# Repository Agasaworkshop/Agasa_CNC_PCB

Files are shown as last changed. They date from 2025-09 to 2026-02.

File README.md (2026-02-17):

# PCB MILLING CNC OVERVIEW  



I've decided to make this CNC from spare parts to see if I was up to the challenge. This was very time-consuming, and it is still a work in progress, but it is enough for a first publication, to see if people like it and maybe contribute.
****The total cost is around 150€, it also requires several hours of printing and assembly.****  
[Here you can find a video about it](https://www.youtube.com/watch?v=syjpmd4Yy7Q)

This project aims to create an affordable CNC that can be built with many common parts you might already have lying around: [here you can find the bill of materials.](https://docs.google.com/spreadsheets/d/1UYvKP2MYEV8sfaGlQmCoOGCL_2WACBQjZGL0-ml8eyc/edit?usp=sharing)

This project also needs some tools like:  
- A soldering iron
- Something to cut M8 and M4 threaded rods, like a hacksaw or Dremel (or even a bolt cutter for the M4 rod)
- M3 and M1 allen key (usually provided with the screw sets and collet).
- M8 wrench.
- Common household supplies like tweezers and scissors.
- A drill (even a weak one) to drive the M8 rods into PLA pieces and make holes.
- A hammer + small screwdriver (it is sometimes useful to drive the M4 rods into the PLA).
- Phillips screwdrivers for the screw terminals of the relay and motor driver.
- A hard brush to clean up the boards after milling. 

This machine is made to accept two common formats of copperclad board I can find online, which are 10x7cm and 5x7cm.
It is a relatively slow machine ([but it could be improved](https://github.com/Agasaworkshop/Agasa_CNC_PCB?tab=readme-ov-file#plans-for-upgrades)), and results also depends on the board quality.  
It is also very loud and requires eye protection, ear protection, and a respirator mask.

Here is a quick preview of the process of making a board (more info below):

| Step | Description | Time taken | Needs operator surveillance |
|:---|:---:|---:|---:|
| Make the PCB | use [Kicad](https://www.kicad.org/) or some other software to make the gerber files | depends on the board | Yes |
| Convert Gerber to CNC files | use [flatCam](http://flatcam.org/) (or similar) to export a gcode with the proper format | 3 minutes | Yes |
| Jog the machine to the starting point and change the bit | use gcode and the commands to set a relative origin, enable plane probing and change the bit | 5 minutes | Yes|
| Start milling | Use the commands to start the route.cnc file** | 6 minutes for plane probing and 22 minutes for the example PCB(the loud part) | No|
| Jog the machine to the starting point and change the bit | use gcode and the commands to set a relative origin, disable plane probing and change the bit| 3 minutes | Yes|
| Start drilling | Start the drill.cnc** file | 8 minutes for the example PCB | No| 
| Jog the machine to the starting point and change the bit | use gcode and the commands to set a relative origin and change the bit| 5 minutes | Yes|
| Start cutting | Start the edge.cnc** file | 20 minutes for the PCB shown*| Yes |
| Add UV mask | I would not advise making this on the CNC, I did try a bit  but it is not worth it time-wise | 10 minutes [(without CNC)](https://youtu.be/wvU2yyfH-XE?si=ILHJE20edIJDHiam) | Yes |  

*I was afraid to go too fast, so I didn’t stress test this. I used 0.3 mm passes at 250 speed (31% of max) with a 2 mm bit not meant for PCBs. Test with caution.  
**You can also run other file names. I made some specific names and commands to make it quicker for my testing. 

Here are the PCBs I refer to  


  

The third one was done by milling the solder mask, but I do not recommend it as it is quite unreliable. 

Here are some standard results on FR1 board made with the latest release (note that you can get better results, but I tried to ensure reliability):

(they all work fine)

## What to expect
I REALLY do not want to deceive anyone, this machine is not perfect at all.  

This was a project made to challenge myself and allow me to make PCBs at home, the process is a bit convoluted, the arduino code could be less clunky (even though I am limited by the Arduino Nano’s memory, I should migrate this project to a more capable board in the future).  

When drilling holes they tend to be slightly off center, it might be due to some imperfections, it does not seem to stack over time tho. 
In previous versions of the Z rails I had some problems losing some steps over long incisions but that is no longer the case.  
For reference, this is a 50-minute incision, this is close to the maximum this machine can do

Here is the board:  


Due to the size of the board, I suggest cutting deeper to ensure proper isolation. This worked reasonably well, but I had to refine 5 pads with a box cutter. (I used –0.15 mm to be sure, that is why some traces are a bit deep, I might also suggest using a 0.2mm bit and not a 0.1mm bit, especially if you don't use a soldermask to avoid bridging while soldering).  

There is also some kind of distortion (not related to lost steps) that causes some traces to deform, this is usually harmless unless it happens on the segment that closes the shape, to prevent this from causing problems I've added the "add squares" option to the patcher. It seems to work fine.   

Here you can see a board that was also cut with this machine(the bit was a bit out of whack here tho).   
    
This board is the [Detective Boys walkie talkie pin badge](https://github.com/DanieElectronics/DetectiveBoysWT) from [DanieElectronics](https://github.com/DanieElectronics)

# Assembly
Being a budget machine, it requires considerable effort on the user's part for assembly.  
Additional hardware notes can be found [here](HARDWARE_NOTES.md).
## Frame
The frame is made of hollow PLA segments reinforced with M8 threaded rods and filled with concrete.  
This creates a very rigid structure with decent tolerances, good vibration damping, and low cost. The M8 rods also help with assembly.  




## Axes
Describing the assembly of each small piece in detail would be complex and not very clear. That’s why I prepared four files: Preview.blend, Preview_x.blend, Preview_y.blend, and Preview_z.blend—each containing all 3D printed pieces and hardware in their correct positions, with [color-coded](https://docs.google.com/spreadsheets/d/1UYvKP2MYEV8sfaGlQmCoOGCL_2WACBQjZGL0-ml8eyc/edit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) hardware. 
Apply grease to all screws and guides.
Unfortunately, I am dumb enough to model in blender.  
I didn’t find a better way to display the assembly, so you will need to [download Blender](https://www.blender.org/download/) (free) to view the files.  
This also means I don’t have convenient CAD files for the project. Even the STL files come from messy Blender projects, so I will consider the STL files themselves as the source for licensing purposes.  





### Y axis
Due to the way it is mounted this axis requires a bit of care, you'll have to adjust it so that the rails are pretty consistently spaced (use a caliper to check).

### Bellows
Unfortunately, this was a bit rushed.   
You can print the bellows flat on your bed with a 0.12mm layer height.   
This will result in a sheet that can easily be folded back and forth to make the bellows. I did not add some of the features to make them easier to detach from the plate, but they can be easily cut out.   
[Here  you can find some more information on how I installed them.](Bellows.md)  

## Electronics
The electronics require some work, but it should not be a problem for anyone building PCBs.  
Here is the list of boards I used:  
3x ULN2003 stepper motor driver  
1x micro SD card reader  
1x Arduino Nano  
1x LM2596 DC to DC Buck Converter module   
1x relay module  
1x custom board (see below)  
1x custom board to distribute power (just a couple of lines of solder with all the cables going out to the various modules)
1x metal M3x10cm washer used for the motor.  
1x metal washer with a bigger diameter used on the bed.  

-I power this with a computer power supply (the 12V line). I suggest using this type of power supply, as they can be obtained cheaply or even for free from old computers and online marketplaces such as eBay or Facebook marketplace.   
-Power the ULN2003 with 12 V, along with the motor driver and the step-down module (if you use a computer PSU, you can simply connect the 5 V line).   
-Set the step-down output to 5 V, and connect the Arduino, relay, and SD card boards to it.   
-The relay is used to switch on and off the motor driver.      
-The motor driver is connected to the motor with a flyback diode and large capacitors rated for more than 12 V.    

This is the pinout of the Arduino:  

| Arduino pin | Conn. | Arduino pin | Conn. |
| :---: | :---: | :---: | :---: |
| TX1 | NC | D13 | SCK sd card board |
| RX0 | NC | 3v3 | NC |
| RST | NC | REF | NC |
| GND | OUT- stepdown | A0 | MZ IN4 |
| D2 | MY IN4 | A1 | MZ IN3 |
| D3 | MY IN3 | A2 | MZ IN2 |
| D4 | MY IN2 | A3 | MZ IN1 |
| D5 | MY IN1 | A4 | Relay S |
| D6 | MX IN4 | A5 | Z2 enable pin custom board |
| D7 | MX IN3 | A6 | switch pin on custom board  |
| D8 | MX IN2 | A7 | Z2 pin on custom board |
| D9 | MX IN1 | 5V | OUT+ stepdown |
| D10 | CS sd card board | RST | NC |
| D11 | MOSI sd card board | GND | NC |
| D12 | MISO sd card board | Vin | NC |  

NC = not connected  
MX = ULN2003 connected to the x motor  
MY = ULN2003 connected to the y motor   
MZ = ULN2003 connected to the z motor   

To check all the limit switches and the contact between the board and the motor with a few pins, I have made a little custom board on perfboard.  
Here is the schematic:  
   
I suggest adding connectors (I used JST connectors) at the positions indicated by the red boxes.  

I mounted the electronics with my [CMS](https://www.printables.com/@AgasasWorksho_391302/collections/863243) system on a printed plate (that you can find in the files)  

  

Alternatively, you could put together the circuit on perfboard like shown here:
   
Using the kicad files might help making this. 

Once the machine is ready, you could mill your own board:   
  
This board will be uploaded under the name "single sided PCB".  
Here it is mounted and working:  
   
I would advice using the board from PCBway below as a reference for the components, in alternative you can use the kicad file.  

Probably the most convenient way of doing this would be to buy one from [PCBWay](https://www.pcbway.com/) from the start, in fact they kindly sponsored me and provided me with some boards to test and I was really happy with the product, they are really well made quality boards (and I know a thing or two about making PCBs at this point) here they are, I will upload them as "double sided PCB"   
  
    
Note that I messed up the capacitor silkscreen and it's flipped, the files I upload will be corrected.   
[Here you can find the list of components.](https://docs.google.com/spreadsheets/d/1UYvKP2MYEV8sfaGlQmCoOGCL_2WACBQjZGL0-ml8eyc/edit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)  

How the washers are  mounted:   
   
You can solder tin to steel; it will flow nicely once the washer reaches a sufficient temperature. This may take some time, during which the solder will not adhere.  

# Using the machine
The code does the minimum required to make the machine work. It can read some G-code, probe the plane to compensate for a skewed board or other imperfections. Here is the list of commands:  
1 + {Gcode} = executes that Gcode.  
2 = Saves the current X, Y, Z coordinates to the offset, and considers the current position as the origin.  
3 = writes in the console the X,Y,Z coordinates, the offsets and some more stuff.  
4 = lowers the Z axis until it finds contact.  
5 = starts the "route.cnc" file.  
50 + "file_name.cnc" = starts the "file_name.cnc" file. For example, 50 route.cnc is equivalent to command 5 (max 16 characters).
51 = starts the "mask.cnc" file. It does not disable plane probing and does not perform probing; you need to have done the previous probing. (Do not shut it down after route.cnc).
52 = starts  the "drill.cnc" file, disables plane probing.  
53 = starts  the "cut.cnc" file, disables plane probing.  
6 = tries to initiate the SD card (also done at start).  
7 = prints SD card content.   
8 = homes the Z axis alone.   
9 = toggles plane probing.   
10 = toggles debug mode, which enables moving without homing.   
11 = toggles enabled and disabled holding torque.  

❕Note that the 51/52/53 commands are already tailored for their purpose and should not need you to toggle plane probing, if you use the 50 command you must disable the plane probing if you don't want it (for example if you decided to make a different drill_1.cnc file make sure to have plane probing off).

Change relative system  
21 = save solder mask relative system.  
22 = save drill relative system.  
23  = save cutting relative system.  
211 = load solder mask relative system.  
221 = load drill relative system.   
231 = load cutting relative system.  

The machine currently cannot change spindle speed. You can manually adjust it on some motor drivers. I always run it at 100%. I plan to update this; it should be fairly simple, but I’m burned out.  
The machine currently only recognizes  
G00/G01  (movement)  
M03/M05  (spindle on/off)  
G28  (home all axes)  
M220 (change stepper speed, for example "G220 80" (or "G220 S80 it's the same) will set the G01 speed as 80% of the G00 speed which is considered the fastest speed (can't go over 100% or under 0%)  
I did attempt some extra features, but the Arduino Nano is already running out of memory.  

## How to prepare the files
- Create the gerber file.  
- Import the gerber files of the engraving, holes and cuts in flatcam.  
- Select the engraving, go to isolation routing, and set the bit thickness (I use 0.1 mm, sometimes 0.2 mm). Generate the geometry and set the bit as a C-bit (even if it is actually a V-bit). Then select a cutting depth. Different boards may require different values, so you will need to experiment. On FR1 boards, a depth of -0.1 mm produced good results.   
- Set the end move and tool change Z to a low value to avoid exceeding the limits, then generate the CNC object and save the file as route.cnc. Open the CNC_file_patcher I provided and drag the file onto it; it will be patched for this machine. (Note: you can name the file anything if you plan to use the 50 command, up to 16 characters.)    
- Select the drill file, set the tool change Z and end move to 3 mm, and set the cutting depth slightly less than the PCB thickness (I use -1.35 mm on 1.4 mm boards). This prevents damaging the bed, but you will need to complete the holes manually. It is a simple and quick task. Save the file as drill.cnc (you can choose any name if you use the 50 command).   
-  Select the edge file, set the bit diameter, and use the same depth as for the drill file. I used -0.3 mm passes to avoid stressing the machine. Export it as edge.cnc (you can name it freely if you use the 50 command).   
-  Select the mask file, set the bit diameter, and use the paint tool. Set an offset—0.5 mm is recommended—but check that the mask is fully cut out given your bit diameter. The software will skip areas that are too small for the bit plus offset. Export the file as mask.cnc (you can name it freely if you use the 50 command).    

## How to operate the CNC  
‼️‼️You MUST wear personal protective equipment (PPE) when operating this machine, including eye protection, ear protection, and a respirator mask (especially for edge cutting and drilling). Work in a well-ventilated area, particularly when using FR4 boards or performing cutting operations (I don't even really recommend cutting FR4, just engraving and milling). 
 
Use commands prefixed with M only if you plan to mill the solder mask, and N only if you do not plan to mill it. Note: milling the solder mask is not recommended.    

!!As it stands, disconnecting the computer and reconnecting will lead to the Arduino resetting and losing the ability to keep going with what you were doing. Use a reliable method; I found out my phone is great at this; it can go into standby and still not lose the serial connection, and thus not reset the Arduino. 

- 1) Power up the machine with the external power supply and connect your computer or phone.  
- 2) Secure a board with all bolts, make sure the bed washer is tight. Forgetting this may damage the bit.   
- 3) Before moving, you must home the machine (it will not accept movement if not homed). Send the following over serial at 9600 baud: "1 G28". Here, 1 indicates that the following command is G-code, and G28 is the “home all axes” command.    
- 4) Jog the machine to the desired starting position using G00 (rapid movement). A good starting point is the bottom-left corner, approximately at X20 Y20. For example: "1 G00 X20 Y20".  
- M5.1.1) Secure the mask milling bit and use the 4 command to bring down the motor to the copperclad board. Save the mask relative system with 21 and home the Z axis with the 8 command.   
- M5.1.2) Secure the drilling bit and use the 4 command to bring down the motor to the copperclad board. Save the drill relative system with 22 and home the Z axis with the 8 command.  
- M5.1.3) Secure the cutting bit and use the 4 command to bring down the motor to the copperclad board. Save the cutting relative system with 23 and home the Z axis with the 8 command.  
- 5.2) Secure the engraving bit and use the 4 command to bring down the motor to the copperclad board. Save the current position as a new origin with the 2 command.
- 6) Enable plane probing with the 9 command. It should say "Prob:on" in the console.  
- 7) Start the engraving process with the 5 command. (or 50 + file name if you named the file differently)
- 8) Wait for the engraving to finish, in my experience, it is relatively safe and hands off but really loud.  
- 9) Remove the dust with a mini vacuum cleaner.  
- M10) Mount the mask milling bit. Load the relative system with command 211. Go to the starting point. Since you saved the relative system in step 5.2, use "1 G00 X0 Y0".   
- M11) Start the mask milling with 51, set the motor speed to 3% (to mill the mask you will need to be able to control the motor).  
- M12) Wait for the mask milling to compòete. This is also hands off, less loud tho.
- 13) Mount the drilling bit, set the speed to max again, disable plane probing with the 9 command.  
- M14) Load the drill relative system with 221 and go back to the origin (1 G00 X0 Y0).  
- N14) Go back to the origin (1 G00 X0 Y0). Lower the z axis with the 4 command and set a new relative system with the 2 command.  
- 15) Start the drilling process with the 52 command.
- 16) Wait for the drilling to finish. In my experience it is relatively safe and hands off but really loud.  
- 17) Remove dust.  
- 18) Secure the cutting bit.I suggest a 1mm cutting bit  
- M19) Load the cutting relative system with command 231. Set the feed speed* and return to the origin using "1 G00 X0 Y0".  
- N19) Lower the z axis with the 4 command and set a new relative system with the 2 command.  
- 20) Start the cutting process with the 53 command.  
- 21) Wait for the cut to finish. While you're at it keep an eye on it, and remove some dust. I suggest moving it with a brush and vacuuming it off the board.
- 23) Dismount the board. Scrub it with a hard brush, check continuity, drill out any remaining holes and complete the cut with a box cutter.
- N24) Add the solder mask like in [this video](https://youtu.be/wvU2yyfH-XE?si=ILHJE20edIJDHiam).

❕❕Every time you secure a new bit, you will have to check for the runout. I just look at it and spin it slowly to check, this is very finicky; it will depend on the quality of your coupler or collet.  
I still fight a lot with my coupler to get it right. Sometimes it looks fine, but it isn't. It's the biggest problem for me, and it would be solved just by finding good quality 3.17mm couplers, I yet have to find them tho.  
You can find some more details on this [here](HARDWARE_NOTES.md).

*You can set the speed of the G01 command via the M220 command, with a 1mm bit. I have seen you can actually go 100% speed at 0.3mm passes. I would still go a bit lower, like 80%. 

## Post processing
I scrub the board vigorously with a hard brush, which usually suffices. In some cases, I used 500-grit sandpaper (for metals) to fix poorly isolated pads. The process takes less than a minute in total.  
I do advise checking for continuity on your board always.  
In the worst-case scenario, you can use an X-Acto knife or box cutter to fix traces. I have worked extensively to avoid this, so it should not be necessary most of the times.  
Soldering without a solder mask is a harrowing process, so I would advise adding it as shown [here](https://youtu.be/wvU2yyfH-XE?si=ILHJE20edIJDHiam). I am not satisfied with the results of milling the mask myself, although performance depends greatly on the quality of the spring-loaded bit.  

## File patcher   
   
   
The file patcher accepts a file (simply drag and drop it onto the window), patches it, and overwrites it with the new version. Currently, it has five features that you can toggle:  
- Split segments: subdivides long segments into shorter ones (maximum 2 mm). This improves plane compensation, as the software currently creates four planes to approximate the board. Long segments spanning multiple planes can cause inaccuracies.  
- Add overlap: adds some overlap between the end of a trace and its start to improve the likelihood of correct isolation. Copper can sometimes deform and leave a bridge.
- Improve pads: merges close lines of adjacent pads to reduce the probability of ripping off the pad (especially useful for small pitches like 0.5mm). This does not currently work well with the overlap so I made it so that it toggles between the two. This feature is currently limited to horizontal and vertical pads. 
- Add squares: Add squares: due to some errors (possibly bit flexing or play in the axis), the tool may fail to properly reconnect when closing a shape. To improve reliability, this option adds a very small square at the end to ensure a proper cut.
- Extra squares: makes the square bigger to make sure. If they are problematic, the small squares are usually enough.
- Simplify shapes: this could speed up the cut a bit.  
Recommended settings are pre-checked by default.  
I plan to add the ability to customize the squares and other features in a future update.  

# Plans for upgrades
I decided to finalize the current version of the project to take a break, but I still have many improvements I want to implement.  
Here are some potential upgrades:  
1. One could tinker with the speeds, I pushed the x and y motors quite a bit already but I did not consider the z speed to be that impactful on the time. 
2. Considering the little additional cost of NEMA motors, one could decide to mount a pancake NEMA17 motor to the Z and X axis and standard NEMA17 to the Y axis. The code should be fairly simple; I would mostly care about fitting nemas to X and Y and try to get a better speed.
3. I've tested quite a bit with milling the solder mask and did not have perfect results. I currently suspect my DIY bit is not up to the task. I should investigate further but it felt like a fool's errand, knowing the other way of adding the solder mask.
4. I've fitted the bellows at the end and did not do the best job. I would love to improve on them.
5. Currently, the spindle is very loud. I'd like to figure out if I can do something about it.
6. The current spindle speed regulation is crude. If you skip milling the mask, a single speed suffices. Adding an H-bridge would simplify speed control (the motor draws about 2.5 A).  
7. I would like to test different types of plane probing to maybe make it quicker (it currently takes a total of 25 points 5 at each spot, maybe I could do just 1 for each spot).  
8. I did not tinker enough with the cutting speeds because I was a bit afraid of wrecking the machine at the finish line. I'll have to test a bit after I recover from burnout. 
9. I might want to migrate the code to a better microcontroller. I used arduino to be more accessible but its limitations did show.
10. I tinkered with adding a saving system to avoid homing all the times and to avoid losing progress if one ended up resetting the Arduino by accident. The problem was the arduino memory that was running out.
11. If I do end up changing some of the above, I would probably implement some extra G code, like spindle speed.
12. Find the best working coupler to get good alignment every time; it's the biggest problem for me.
13. I could also consider adding alignment holes to the bed to try implementing double-sided boards.

# Disclaimer
This machine involves mechanical, electrical, and operational risks. I strongly recommend using appropriate personal protective equipment (PPE mentioned above) and ensuring proper ventilation during operation.  
Keep your hands and body parts away from moving axes and the cutting tool, as the system can generate significant force.  
Be careful when wiring the power supply, especially when working with mains voltage.

This project is not certified for compliance with any safety or regulatory standards. By building, modifying, or operating this machine, you acknowledge and accept that you do so entirely at your own risk.
I shall not be held liable for any injury, damage, loss, or legal issues resulting from the use or misuse of this project.

## Extra
- This machine operates on two sizes of boards, which are 5x7 and 10x7. [I've made a little jig to score and snap the boards](https://www.printables.com/model/1377196-107-pcb-splitter), it works well with FR1, not too well with FR4 (it isn't impossible tho).  
- I did attempt some backlash compensation with disappointing results; the current code still has the remains of that (but the parameters are set to 0).

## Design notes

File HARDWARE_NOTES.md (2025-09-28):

# I've experimented quite a bit with different hardware and configurations. I would like to share my findings and ideas here:

## Collets:  
  
Here are all the collets (all 3.17mm to 3.17mm couplers or collets) I've tried:  

1. The hole had quite a big tolerance; the bit ended up being wonky most of the times it was very frustrating to correct.  
2. Same as 1  
3. It was too tight, I could not fit the bits.  
4. It had similar tollerances to 1 and 2 but the coupler nature makes it a bit easier to adjust, it's also quite heavy.  
5. This fit the bit perfectly, the only problem was that it was too tall, this prevented me from mounting.   
6. This is my current choice, it has similar problems to 4 but it's quite a lot lighter and a bit smaller.

I suggest marking one side and tightening mostly that side to both motor shaft and cutting bit to improve probability of working.  
EVERY TIME you change bit you need to check for runout, I don't have anything fancy I jsut spin the bit with my fingers and check if I see it wobble.   
Rule of thumb: if you think there is an imperceptible wobble but you're not sure, there probably is.  

## Motor springs:
These cheap stepper motors have quite a bit of play on the shaft, at the start I tought with the forces involved and the vibrations it would have been necessary to fit very stiff springs, turns out you don't need much.
I strongly suggest quick release skewer springs from bikes, they are very weak and they have the right dimensions, the larger side should be facing the motor. I've tested (and am currently running) much stiffer tower springs
and I did not notice any difference, I am a bit afraid they will wear out the motor quicker but I can't be bothered to change them back.  

## Possible alternative motors:
I've found a couple of alternative stepper motors that could fit this machine. With minor modifications you could even fit fit NEMA17 motors, this would require changing the drivers and code a bit tho. 
I've also found similar motors to these common 28byj-48 with all metal gears, those might be a good upgrade.

## Motor driver:
I'm using a relay with a big DC motor driver I had lying around but it's overkill and cluncky, one could probably fit a much cheaper and effective driver that could be piloted with the same pin as the relay and allow 
for the addition of a speed command, I will work on that in the future.

## Motor to leadscrew couplers:
I've tested a couple, I am currently mounting the clamp style ones but I think the ones with grubscrews would be better. I think the springy ones are not too good for this application I would avoid those. 

Example images of these couplers (source: AliExpress listings):
Springy couplers:  
   
Clamp style coupler:  
  
Recommended couplers:  
  

## Cutting bits:
There are a lot of different kinds of bits. I've found these to be the best (most reliable and durable):  


## Electronics:
I've tried a couple of different configurations; my CMS setup was the easiest to mount but pretty messy.  
I've also tested with making it with perfboard, it took me a lot of time to make, I don't really thinK it was worth it. If you still want to try this route the pcb I designed should be a good reference.  
I've also made a custom PCB, you could pay a service to make you one or, after mounting the machine with a different setup mount it yourself, I'll incluede a CMS module for this board in the files.  

In my design I've used 3 ULN2003; one could consider using only 2 but I did not want to push the current limits of the ICs and just decided to copy the cheap common boards. It is also quite improbable you have 3 motors and only 2 drivers.

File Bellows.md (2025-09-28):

# How to mount bellows  
This, unfortunately, is one of the weakest parts of this build. These parts are quite important to keep dust away from your sensitive lead screws and linear guides.  
In the future, I plan to mount all of them with M3 screws but as of right now you need to hot glue some of the bellows.

# Printing the bellows
You need to print these flat on the bed with 0.12mm layer height, you should get only two layers. After printing you need to bend it back and forth.

# Y bellow
Print two bellows, you will have one at each side of the carriage.
Thread the fishing line (or other wire) through the holes of the bellows and pass it through the hole in the rod holder, do this for both sides then clamp both the wires and the bellow with a screw fixed to the heatset insert of the rod holder, use two pieces of wire, cut them long and refine it later.  
To fix the other end to the carriage hotglue them, you can also cut it a bit with scissors if convinient.  
You should try to get them so that the bellow when folding tends to go down a bit.   
(You can also always glue the rod holder part too of course)   

   

Lateral view   

   

How to glue the bellow to the carriage, note that the piece right next to the glued one bends downwards  

   

How to clamp bellows and strings

Test it by moving the axis in his full range (0 to 90) at the end to see if it folds nicely, try to reposition the glued parts if not.  

# X bellow
This only has glued parts, unfortunately.  
Similar to the Y bellow you need to print two and thread the line, I used only one longer line here looping it around one of the two sides.  
Glue the string at the end of the other side like shown below.  
   

Glue the bellow to the upper lip like here and make sure to get the bellow to bend without raising up like here:  
   

Test it by moving the axis in his full range (0 to 119) at the end to see if it folds nicely, try to reposition the glued parts if not.  

# Z guard
This piece also prints as a flat sheet; bend it in the weak points and secure it to the screw heads like shown:   


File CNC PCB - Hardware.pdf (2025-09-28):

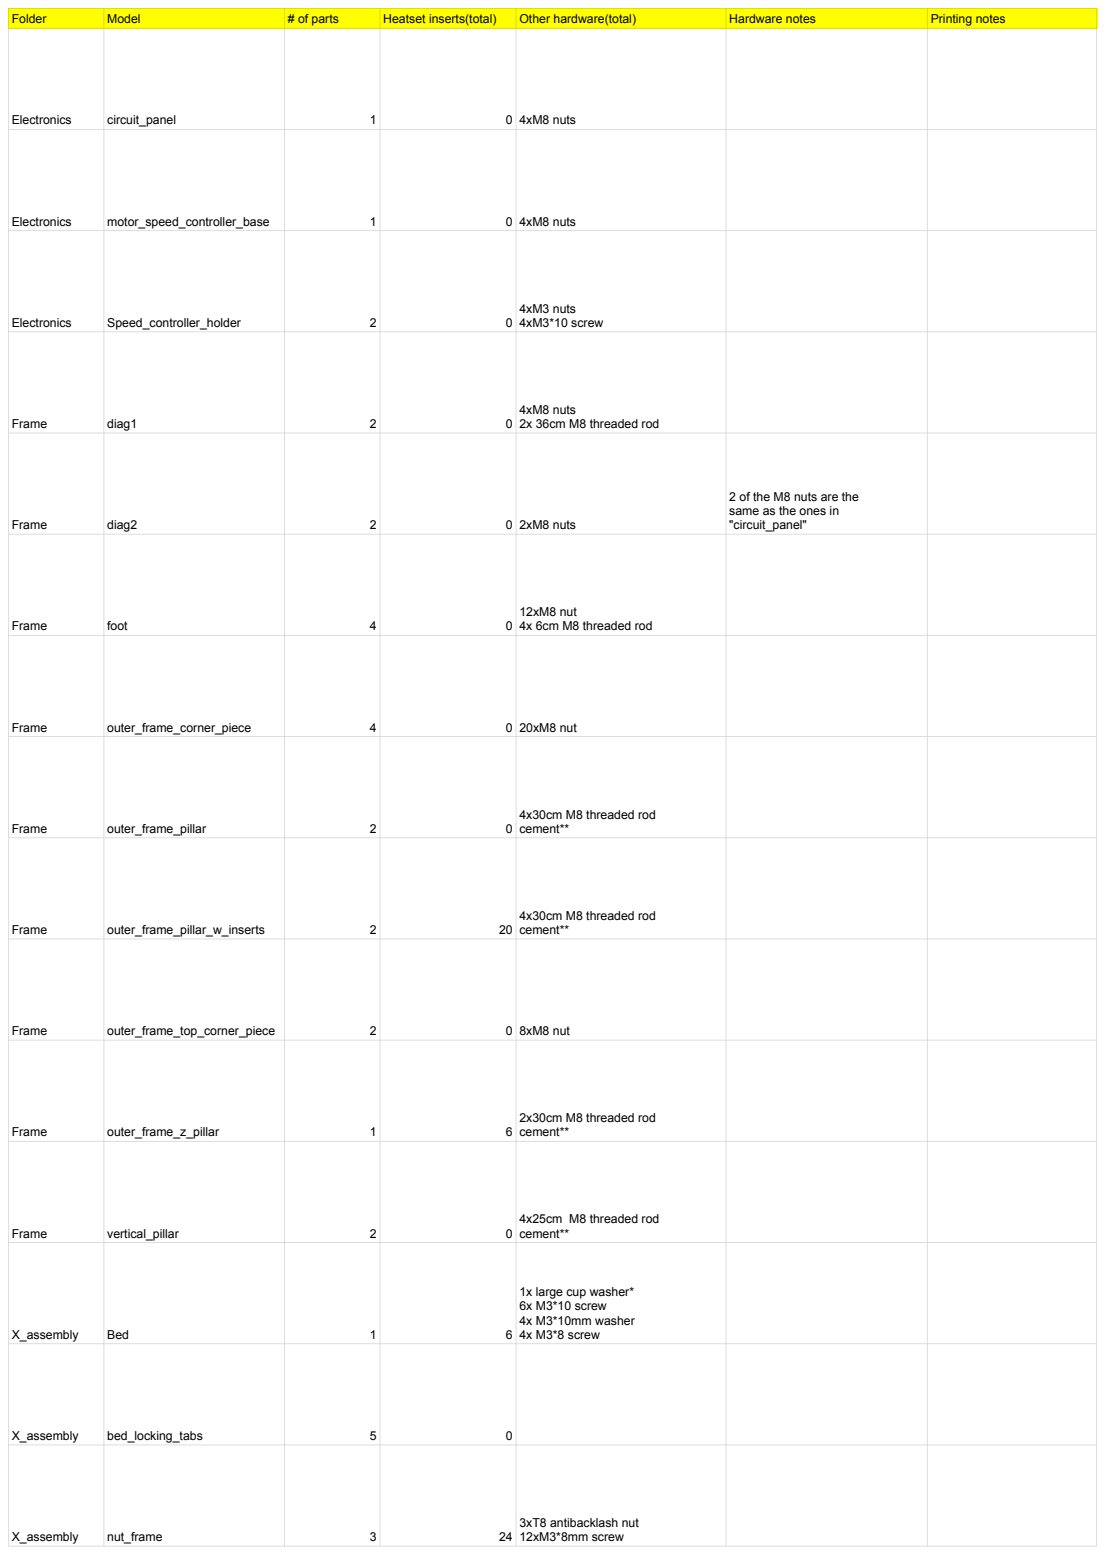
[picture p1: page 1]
Folder; Model; # of parts; Heatset inserts(total); Other hardware(total); Hardware notes; Printing notes; Electronics; circuit_panel; 0 4xM8 nuts; motor_speed_controller_base; Speed_controller_holder; 4xM3 nuts 4xM3*10 screw; Frame; diag1; 4xM8 nuts 2x 36cm M8 threaded rod; diag2; 0 2xM8 nuts; foot; 12xM8 nut 4x 6cm M8 threaded rod; outer_frame_corner_piece; 0 20xM8 nut; outer_frame_pillar; 4x30cm M8 threaded rod cement**; outer_frame_pillar_w_inserts; outer_frame_top_corner_piece; 0 8xM8 nut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

2 of the M8 nuts are the
same as the ones in
"circuit_panel"

1x large cup washer*
6x M3*10 screw
4x M3*10mm washer
4x M3*8 screw

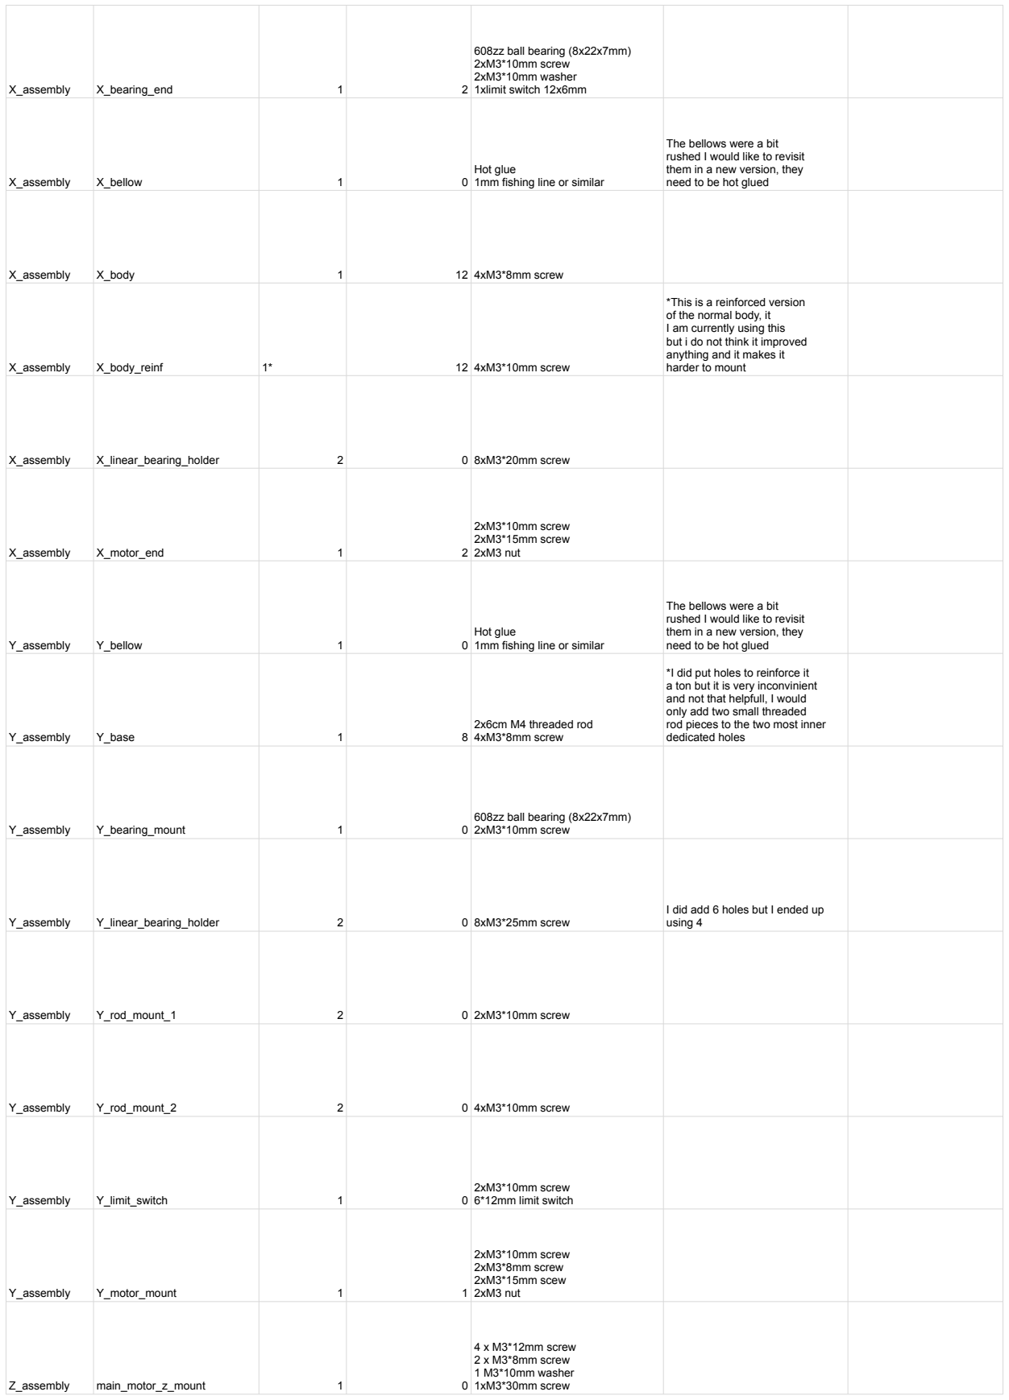
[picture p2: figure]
X_assembly; X_bearing_end; 608zz ball bearing (8x22x7mm) 2xM3*10mm screw 2xM3*10mm washer 1xlimit switch 12x6mm; X_bellow; Hot glue 1mm fishing line or similar; The bellows were a bit rushed I would like to revisit them in a new version, they need to be hot glued; X_body; 12 4xM3*8mm screw; X_body_reinf; 12 4xM3*10mm screw; *This is a reinforced version of the normal body, it I am currently using this but i do not think it improved anything and it makes it harder to mount; X_linear_bearing_holder; 0 8xM3*20mm screw; X_motor_end; 2xM3*10mm screw 2xM3*15mm screw 2xM3 nut; Y_assembly; Y_bellow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

Z_assembly | Z_backplate | 1 | 0 | 2xM4*11cm threaded rod 4xM4*5.5cm threaded rod* 6xM3*15mm screw 6xM3*10mm washer | *you are meant to scew then hammer in the rods to reinforce the plate, it is a bit tedious
Z_assembly | z_bearing_mount | 1 | 2 | 608zz ball bearing (8x22x7mm) 2xM3*10mm screw 2xM3*10mm washer 1xlimit switch 12x6mm
Z_assembly | Z_guard | 1 | 0 | | this folds and clips onto the screws of the linear bearing holder
Z_assembly | Z_linear_bearing_holder | 2 | 0 | 8xM3*25mm scew
Z_assembly | Z_body_reinf | 1* | 12 | 4xM3*10mm screw | *This is a reinforced version of the normal body, it I am currently using this but i do not think it improved anything and it makes it harder to mount
Z_assembly | Z_stepper_mount | 1 | 2 | 2xM3*10mm screw 2xM3*10mm washer 2xM3*8mm screw 2xM3*15mm scew 2xM3 nut
Z_assembly | Z_body | 1 | 12 | 4xM3*10mm screw
total | 121

56 x M8 nuts
2 x 36cm M8 threaded rod
2 x 6cm M8 threaded rod
10 x 30cm M8 threaded rod
4 x 25cm M8 threaded rod
32 x M3*10mm screw
30 x M3*8mm screw
24 x M3*25mm screw
1 x M3*30mm screw
12 x M3*15mm screw
10 x M3 nuts
17 x M3*10mm washer
2 x M4*11cm threaded rod
4 x M4*5.5cm threaded rod
2 x 6cm M4 threaded rod
1 x large cup washer
3 x T8 antibacklash nut
3 x 608zz ball bearing(8x22x7mm) 3 x limit switch 12x6mm
cement
hot glue
fishing line or similar

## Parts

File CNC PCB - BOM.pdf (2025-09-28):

material | # | Price | Notes
Hardware store | | 14,5 | the items below are comprised in this price
gray cement | 2kg
M4x1m threaded rods | 2
M8x1m threaded rods | 6 | | 5 are actually required but you might lose a bit when cutting
M8 nuts | 60
35.7*50mm with 8 or 12mm shaft 12V DC motor (high RPM) | 1 | 6,69
coupler clamp stepper servo motor coupling D20L25 5x8x25mm | 3 | 6 | You should use rigid couplers not the springy ones
28BYJ-48 12V 4 Phase DC Gear Stepper Motor + ULN2003 Driver Board | 3 | 8,49
sd reader | 1 | 1,31
8mm*20cm rods | 5 | 13,01 | you will have to cut one in half or buy 4 20mm and 2 10mm
M3 hex socket scew and washer set | 1 | 6
LM8 LM8UU linear bearing | 12 | 10,14
Arduino nano | 1 | 3
3.17 to 3.17mm coupler | 1 | 2,65 | the price is for 5
PWM Motor speed controller | 1 | 10 | You could easily either skip this or get a way cheaper one
PLA | 2kg | 25 | It should take you less than 2 spools but more than 1, in bundles of 2 spools I can easily find them for 25€ on amazon
DC-DC step down module (12V to 5V) | 1 | 1,79
limit switches 12x6mm | 3 | 1,71 | this is the price for 10 on aliexpress
relay module | 1 | 1,11
12V 10 amp PSU (you should be fine with a bit more than 5) | 1 | 15 | I used a PC power supply, you can easily find them even for free
Bike Quick Release Skewer Springs | 3 | 1,79 | I've also tested stiffer springs with no improvement so these are the best to install and easiest to find
Strong Crystal Fishing Line PE Nylon 0.6mm | 1 spool | 1,59
heatset inserts | 150 | 7,35
T8 lead screw 20cm lead 8mm | 2 | 6,14
T8 lead screw 10cm lead 8mm | 2 | 2,51
T8 anti backlash nut lead 8mm | 3 | 3,64
ball bearing 608ZZ | 3 | 2,69 | the price is for 10
tot | | 152,11 euros
PCB making supplies | # | Price | Notes
0.1mm engraving bits | 10 | 8,42
| | | I suggest using the ones with a spiralized point, they are more expensive
0.8mm drilling bits | 10 | 2,69
Copperclad boards 7x10cm FR1 | 10 | 3,69
Solder mask | 10cc | 2,9
UV nail curing machine | 5
printable transparent sheets | 10
tot | 32,7

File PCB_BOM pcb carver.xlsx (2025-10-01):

Item # | *Designator | *Qty | Manufacturer | *Mfg Part # | Description / Value | *Package/Footprint | Type | Your Instructions / Notes
1 | R1 | 1 | Any | Generic | 1kΩ +/-5% 0.25W | DIN0207 | thru-hole
2 | R2 | 2 | Any | Generic | 9.7kΩ +/-5% 0.25W | DIN0207 | thru-hole
3 | R3 | 1 | Any | Generic | 4.7kΩ +/-5% 0.25W | DIN0207 | thru-hole
4 | R4 | 1 | Any | Generic | 9.7kΩ +/-5% 0.25W | DIN0207 | thru-hole
5 | R5 | 1 | Any | Generic | 9.7kΩ +/-5% 0.25W | DIN0207 | thru-hole
6 | R6 | 2 | Any | Generic | 9.7kΩ +/-5% 0.25W | DIN0207 | thru-hole
7 | C1 | 1 | Any | Generic | 10nF +/-20%, 25V ceramic capacitor | Ceramic Disc 5mm pitch | thru-hole
8 | C2 | 2 | Any | Generic | 10nF +/-20%, 25V ceramic capacitor | Ceramic Disc 5mm pitch | thru-hole
9 | C3 | 1 | Any | Generic | 10nF +/-20%, 25V ceramic capacitor | Ceramic Disc 5mm pitch | thru-hole
10 | C4 | 1 | Any | Generic | 470uF +/-20%, 25V electrolytic capacitor | Radial Ø8 mm 3.8mm pitch | thru-hole
11 | C5 | 2 | Any | Generic | 100nF +/-20%, 25V ceramic capacitor | Ceramic Disc 5mm pitch | thru-hole
12 | C6 | 1 | Any | Generic | 1000uF +/-20%, 25V electrolytic capacitor | Radial Ø8 mm 3.8mm pitch | thru-hole
13 | Q1 | 1 | Texas Instruments | ULN2003AN | Darlington Transistor Array | PDIP-16 | thru-hole | Possibly installed with a socket
14 | Q2 | 1 | Texas Instruments | ULN2003AN | Darlington Transistor Array | PDIP-16 | thru-hole | Possibly installed with a socket
15 | Q3 | 1 | Texas Instruments | ULN2003AN | Darlington Transistor Array | PDIP-16 | thru-hole | Possibly installed with a socket
16 | A1 | 2 | Any | Generic | Female square pin header 1x15 | 2.54mm pitch | thru-hole
17 | J13 | 1 | Any | Generic | Male square pin header 1x3 | 2.54mm pitch | thru-hole
18 | J8 | 1 | Any | Generic | Male square pin header 1x6 | 2.54mm pitch | thru-hole
19 | J1 | 1 | Any | Generic | Connector_JST:JST_XA_B05B-XASK-1_1x05 | P2.50mm_Vertical | thru-hole
20 | J2 | 1 | Any | Generic | Connector_JST:JST_XA_B05B-XASK-1_1x05 | P2.50mm_Vertical | thru-hole
21 | J3 | 1 | Any | Generic | Connector_JST:JST_XA_B05B-XASK-1_1x05 | P2.50mm_Vertical | thru-hole
22 | J4 | 1 | Any | Generic | Connector_JST:JST_XA_B02B-XASK-1_1x02 | P2.50mm_Vertical | thru-hole
23 | J5 | 1 | Any | Generic | Connector_JST:JST_XA_B02B-XASK-1_1x02 | P2.50mm_Vertical | thru-hole
24 | J6 | 1 | Any | Generic | Connector_JST:JST_XA_B02B-XASK-1_1x02 | P2.50mm_Vertical | thru-hole
25 | J7 | 1 | Any | Generic | Connector_JST:JST_XA_B02B-XASK-1_1x02 | P2.50mm_Vertical | thru-hole

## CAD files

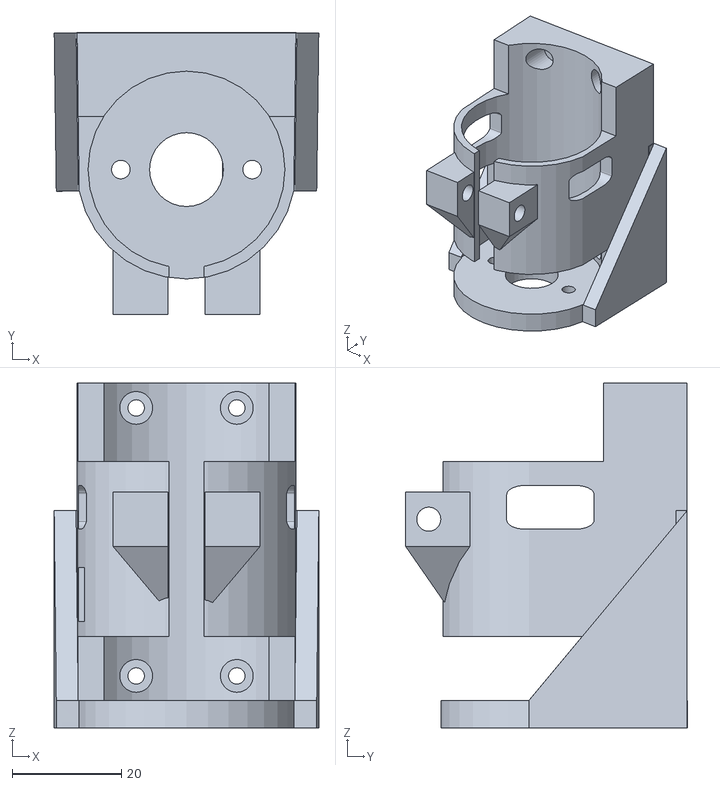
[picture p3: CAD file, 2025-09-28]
release/Z_assembly/main_motor_z_mount.stl
48.4 x 51.5 x 63.1

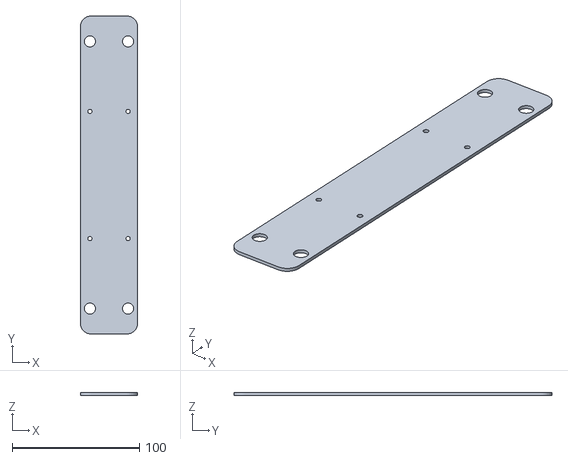
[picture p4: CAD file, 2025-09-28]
release/Electronics/motor_speed_controller_base.stl
45.0 x 250.0 x 2.00

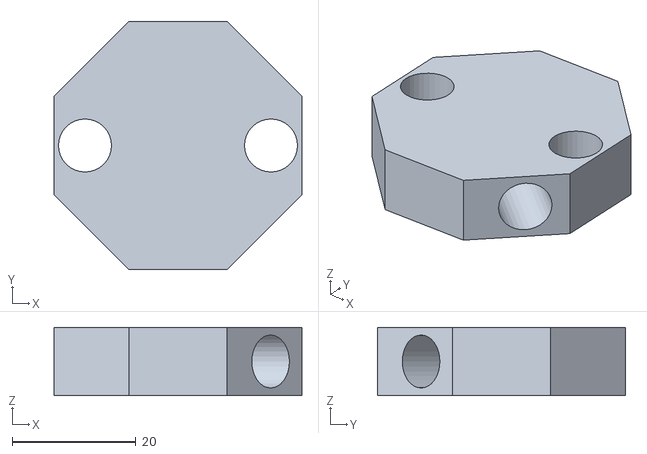
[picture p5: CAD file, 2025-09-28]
release/Frame/diag1.stl
40.0 x 40.0 x 11.0

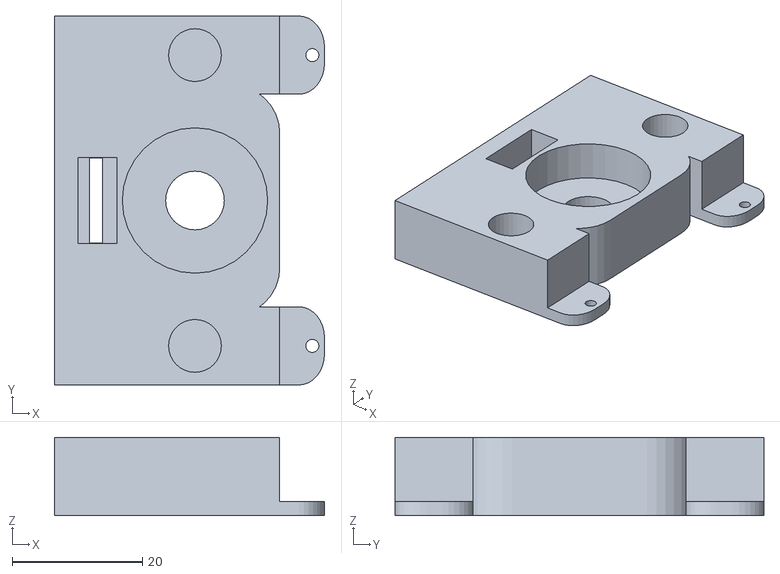
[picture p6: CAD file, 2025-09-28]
release/X_assembly/X_bearing_end.stl
41.4 x 56.6 x 12.0

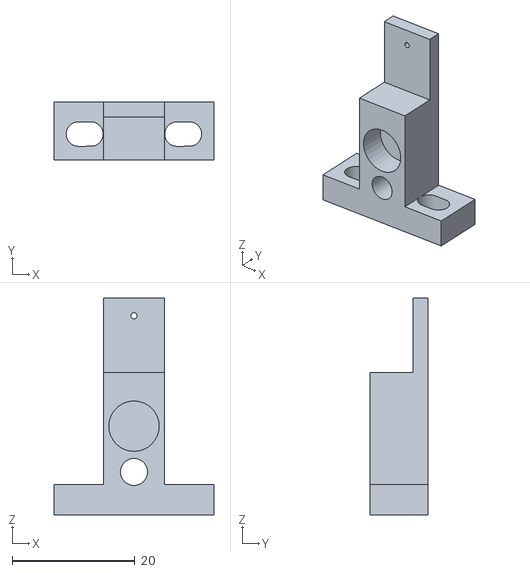
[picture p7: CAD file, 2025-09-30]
release/Y_assembly/Y_rod_mount_1.stl
26.0 x 9.50 x 35.3

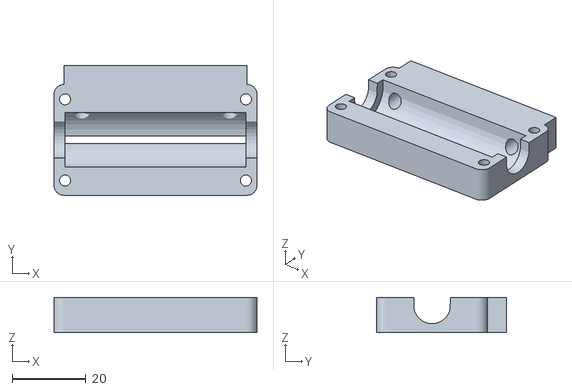
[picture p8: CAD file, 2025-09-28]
release/Z_assembly/Z_linear_bearing_holder.stl
55.0 x 35.1 x 9.50

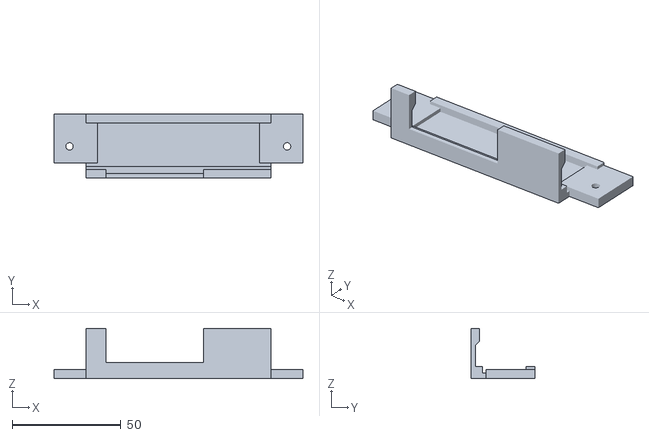
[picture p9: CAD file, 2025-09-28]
release/Electronics/Speed_controller_holder.stl
114.5 x 29.5 x 23.0

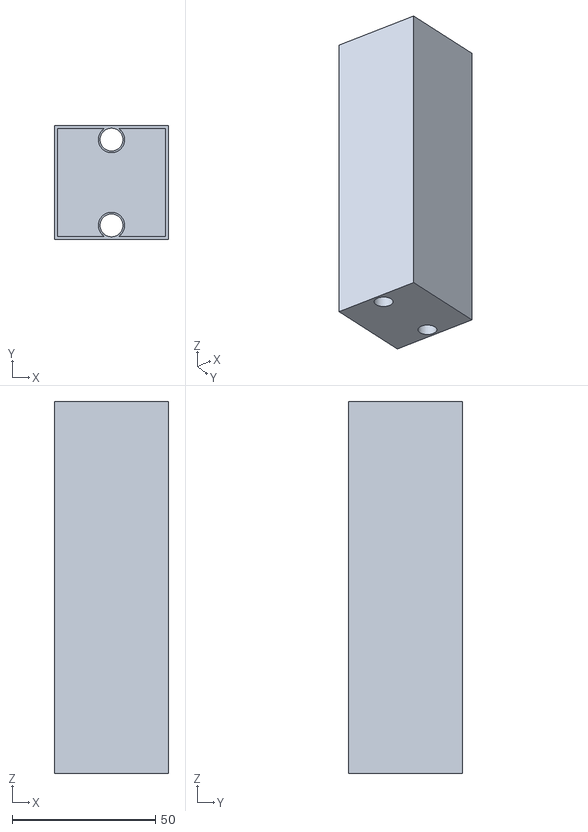
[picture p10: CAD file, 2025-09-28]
release/Frame/vertical_pillars.stl
40.0 x 40.0 x 130.0

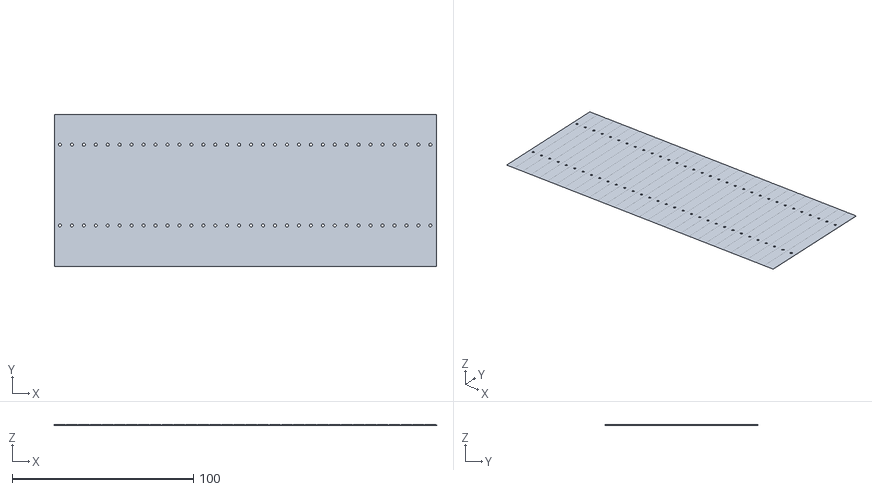
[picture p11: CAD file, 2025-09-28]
release/X_assembly/X_Bellow.stl
211.0 x 84.0 x 0.26

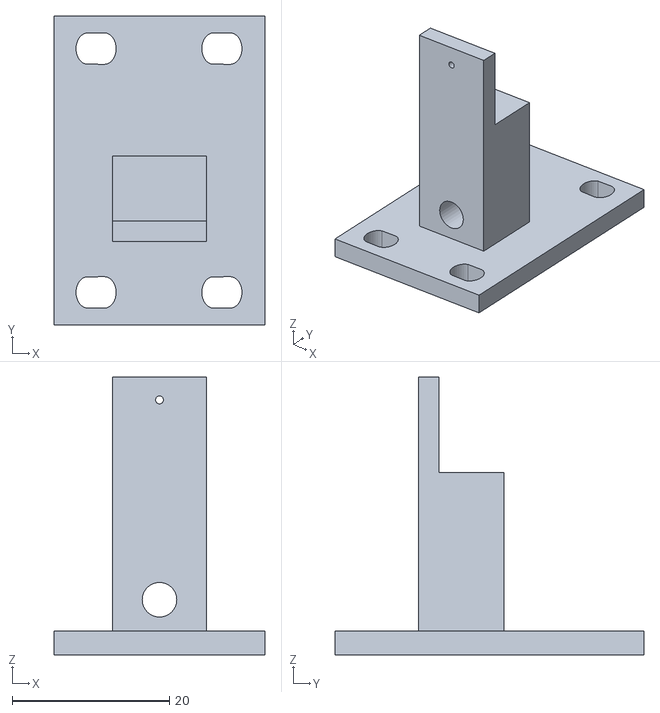
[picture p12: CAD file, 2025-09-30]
release/Y_assembly/Y_rod_mount_2.stl
26.8 x 39.3 x 35.3

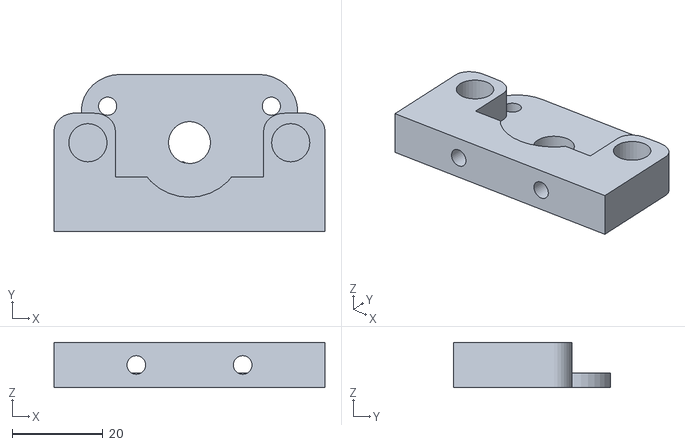
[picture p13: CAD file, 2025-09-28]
release/Z_assembly/Z_stepper_mount.stl
59.6 x 34.6 x 10.0

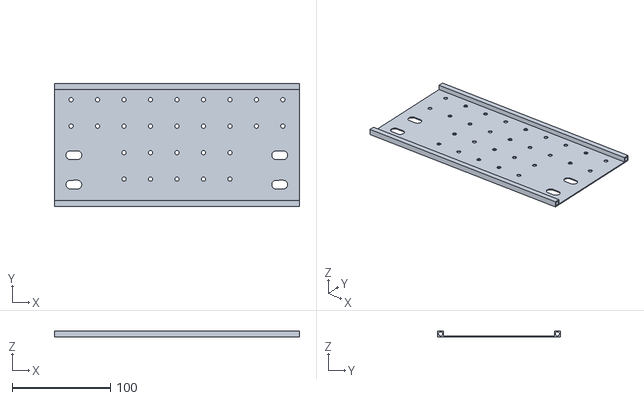
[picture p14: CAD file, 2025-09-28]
release/Electronics/circuit_panel.stl
250.0 x 125.1 x 6.29

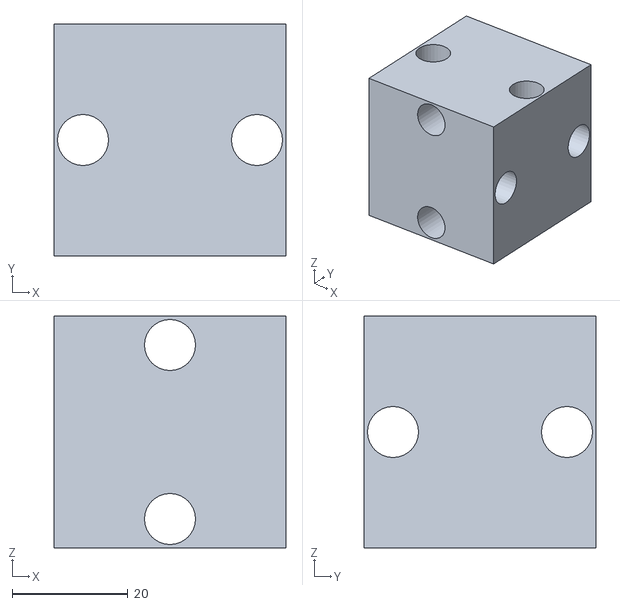
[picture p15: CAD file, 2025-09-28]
release/Frame/outer_frame_corner_piece.stl
40.0 x 40.0 x 40.0

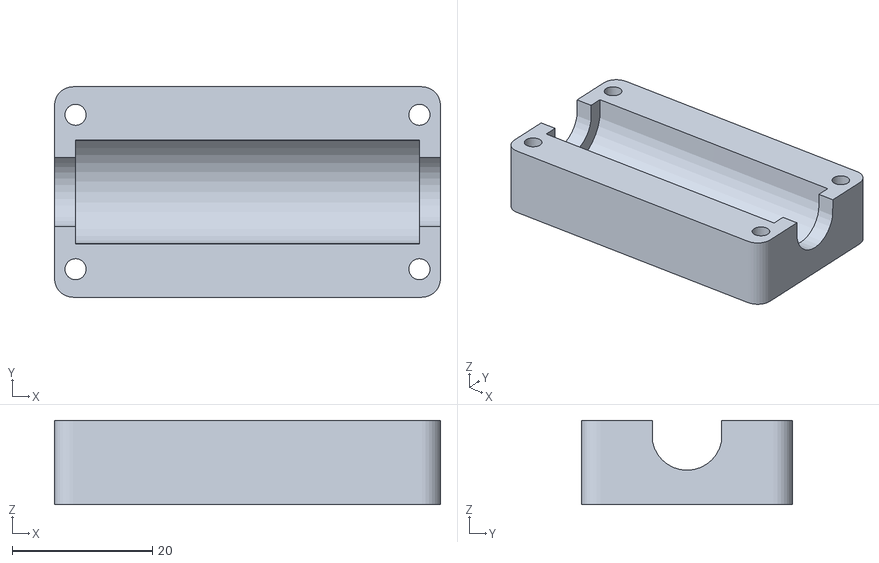
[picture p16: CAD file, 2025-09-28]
release/X_assembly/X_linear_bearing_holder.stl
55.0 x 30.0 x 12.0

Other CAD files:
release/Z_assembly/Z_bearing_mount.stl
release/Frame/outer_frame_top_corner_piece.stl
release/X_assembly/X_body.stl
release/Y_assembly/Y_motor_mount.stl
release/Frame/diag2.stl
release/Frame/foot.stl
release/Frame/outer_frame_pillar.stl
release/Frame/outer_frame_pillar_w_inserts.stl
release/Frame/outer_frame_z_pillar.stl
release/Preview.blend
release/Preview_x.blend
release/Preview_y.blend
release/Preview_z.blend
release/X_assembly/Bed.stl
release/X_assembly/X_body_reinf.stl
release/X_assembly/X_motor_end.stl
release/X_assembly/bed_locking_tabs.stl
release/X_assembly/nut_frame.stl
release/Y_assembly/Y_base.stl
release/Y_assembly/Y_bearing_mount.stl
release/Y_assembly/Y_bellow.stl
release/Y_assembly/Y_limit_switch.stl
release/Y_assembly/Y_linear_bearing_holder.stl
release/Y_assembly/nut_frame.stl
release/Z_assembly/Z_backplate.stl
release/Z_assembly/Z_body.stl
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

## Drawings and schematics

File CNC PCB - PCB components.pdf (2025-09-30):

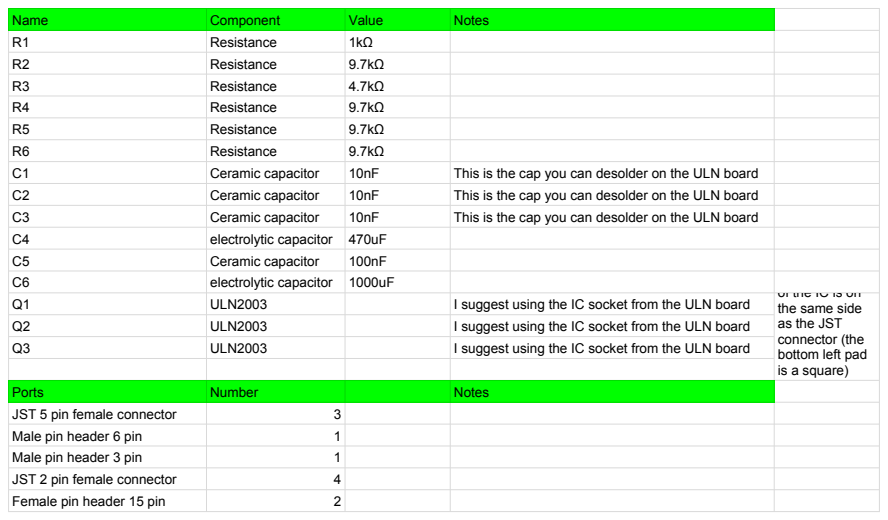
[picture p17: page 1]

of the IC is on
the same side
as the JST
connector (the
bottom left pad
is a square)

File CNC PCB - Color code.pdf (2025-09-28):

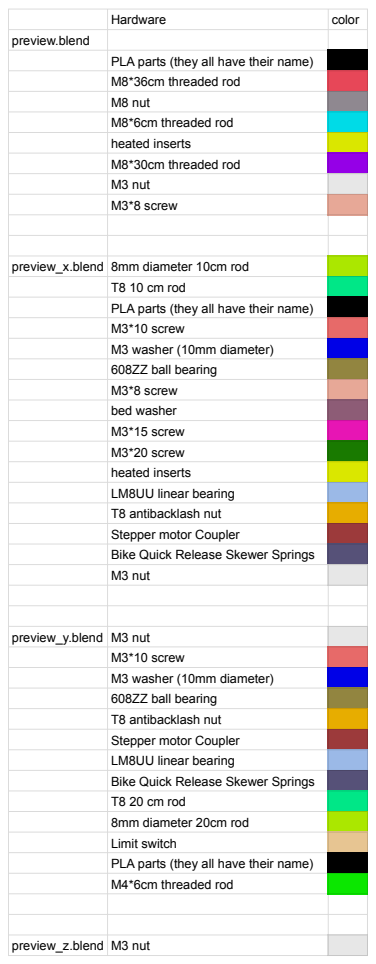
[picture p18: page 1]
Hardware; color; preview.blend; preview_y.blend M3 nut; preview_z.blend M3 nut

PLA parts (they all have their name)
M8*36cm threaded rod
M8 nut
M8*6cm threaded rod
heated inserts
M8*30cm threaded rod
M3 nut
M3*8 screw

preview_x.blend 8mm diameter 10cm rod

T8 10 cm rod
M3*10 screw
M3 washer (10mm diameter)
608ZZ ball bearing
bed washer
M3*15 screw
M3*20 screw
LM8UU linear bearing
T8 antibacklash nut
Stepper motor Coupler
Bike Quick Release Skewer Springs

T8 20 cm rod
8mm diameter 20cm rod
Limit switch
M4*6cm threaded rod

M3*10 screw

M3 washer (10mm diameter)

608ZZ ball bearing

T8 antibacklash nut
Stepper motor Coupler

LM8UU linear bearing
Bike Quick Release Skewer Springs

T8 20 cm rod

8mm diameter 20cm rod

Limit switch
PLA parts (they all have their name)

Spindle

M4 threaded rod 55mm
M4 threaded rod 11cm

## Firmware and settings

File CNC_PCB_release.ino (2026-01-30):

/*Commands
1 + {Gcode} = executes that Gcode
2 = Saves the current x,y,z coordinates to the offset and considers the current position as the origin
3 = writes in the console the x,y,z coordinates, the offsets and some more stuff
4 = lowers the z axys until it finds contact
5 = starts the "route.cnc" file
50 + file name = starts the given file (if present in the SD card)
51 = starts the "mask.cnc" file, does not disable plane probing and does not probe, you need the previous probing (so don't shut it down after route.cnc) <- could be improved
52 = starts  the "drill.cnc" file, disables plane probing
53 = starts  the "cut.cnc" file, disables plane probing
6 = tries to initiate the SD card (also done at start) <- to do
7 = prints SD card content 
8 = homes the z axys alone
9 = toggles plane probing 
10 = toggles debug mode 
11 = toggles enabled and disabled holding torque



Change relative system
21 save solder mask relative system
22 save drill relative system
23  save cutting relative system
211 load solder mask relative system
221 load drill relative system 
231 load cutting relative system 
*/

#include <SPI.h>
#include <SD.h>
#include <AccelStepper.h>
#include <MultiStepper.h>

#define PROBING 3 // 1= taks the lowest point as estimate, 2 = means the 5 points, 3 = mean and filter outliers

void update_limit();
int find_string(char, char[]);
void readline(char[]);
void home_x();
void home_y();
void home_z();
void home_z2();
void file_read(int);
void find_boundaries();
void probe_corners();
int which_plane(long[]);

File myFile;
AccelStepper stepper_x(AccelStepper::HALF4WIRE, 8, 6, 7, 9);
AccelStepper stepper_y(AccelStepper::HALF4WIRE, 4, 2, 3, 5);
AccelStepper stepper_z(AccelStepper::HALF4WIRE, A2, A0, A1, A3);
MultiStepper steppers;
const int steps_per_mm_xy = 512;
const int steps_per_mm_z = 512;
bool limit_x,limit_y,limit_z;
bool ready = false;
bool is_probed = false;
bool plane_probing = false;
bool enabled = true; 
bool alt = false;
long offset_x = 0; long offset_y = 0; long offset_z = 0;
float x_boundary = 0; float y_boundary = 0;
const float max_x = 120; 
const float max_y = 92;
const float min_z = -21.5;
int strikes = 0; 
bool x_backlash = false; bool y_backlash = false; bool z_backlash = false; //indicates the last rotation: to the switch = false, away from the switch is true (away is negative ->true, towards is positive ->false)
const long x_m_backlash = 0; //i segni sono un po' strani, il plane probing tecnicamente in x e y non lo usa, non è così grave credo, è un po' intricato da fixxare
const long y_m_backlash = 0; //-8
const long z_m_backlash = 0; //-8


long offset_x_mask = 0; long offset_y_mask = 0; long offset_z_mask = 0; 
long offset_x_drill = 0; long offset_y_drill = 0; long offset_z_drill = 0;
long offset_x_edge = 0; long offset_y_edge = 0; long offset_z_edge = 0;

long z_map[5];
float plane_coefficients1[3], plane_coefficients2[3],plane_coefficients3[3], plane_coefficients4[3];
int x_y_speed0 = 800; //veloce era 500
int x_y_speed1 = 800; // 250
const int z_speed0 = 500; //500
const int z_speed1 = 140; //140

void setup() {
  pinMode(A4, OUTPUT); //relé
  pinMode(A5, OUTPUT); //limit z2 HIGH when active, this means that the plane acts as a switch only during the probing 
  //A7 is the analog pin that reads the z2, I use two cables to avoid junk on the pin while cutting
  //A6 is the analog pin for the limit switches
  digitalWrite(A5,LOW);
  digitalWrite(A4, LOW);
  Serial.begin(9600);
  Serial.println(F("Hi"));
  stepper_x.setMaxSpeed(x_y_speed0);
  stepper_x.setAcceleration(100);
  stepper_x.setSpeed(x_y_speed0);
  stepper_y.setMaxSpeed(x_y_speed0);
  stepper_y.setAcceleration(100);
  stepper_y.setSpeed(x_y_speed0);
  stepper_z.setMaxSpeed(z_speed0);
  stepper_z.setAcceleration(100);
  stepper_z.setSpeed(z_speed0);
  steppers.addStepper(stepper_x);
  steppers.addStepper(stepper_y);
  steppers.addStepper(stepper_z);

  update_limit();
  if (!SD.begin(10)) { //tries to connect to the SDcard
    Serial.println(F("SD f")); 
  }
}

void loop() {
  if (Serial.available()) {
    int a = Serial.parseInt();
    if (a == 1) {
      String command = Serial.readString(); //I should really just ditch the string but I'm lazy
      command.trim();
      char command_arr[40];
      command.toCharArray(command_arr, 40);
      readline(command_arr);
    }else

    if (a == 2) {
      offset_x = offset_x -(stepper_x.currentPosition());
      offset_y = offset_y -(stepper_y.currentPosition());
      offset_z = offset_z + (stepper_z.currentPosition());
      stepper_x.setCurrentPosition(0);
      stepper_y.setCurrentPosition(0);
      stepper_z.setCurrentPosition(0);
    }else
    
    if (a == 21) {
      offset_x_mask = offset_x - (stepper_x.currentPosition());
      offset_y_mask = offset_y - (stepper_y.currentPosition());
      offset_z_mask = offset_z + (stepper_z.currentPosition());
      Serial.print(F("y"));
    }else
    if (a == 22) {
      offset_x_drill = offset_x - (stepper_x.currentPosition());
      offset_y_drill = offset_y - (stepper_y.currentPosition());
      offset_z_drill = offset_z + (stepper_z.currentPosition());
      Serial.print(F("y"));
    } else
    if (a == 23) {
      offset_x_edge = offset_x - (stepper_x.currentPosition());
      offset_y_edge = offset_y - (stepper_y.currentPosition());
      offset_z_edge = offset_z + (stepper_z.currentPosition());
      Serial.print(F("y"));
    }else

    if (a == 211) {
      long real_pos_x = offset_x - stepper_x.currentPosition();
      stepper_x.setCurrentPosition(-real_pos_x + offset_x_mask); //current position è negativo quindi deve riflettere

      long real_pos_y = offset_y - stepper_y.currentPosition();
      stepper_y.setCurrentPosition(-real_pos_y + offset_y_mask);

      long real_pos_z = offset_z + stepper_z.currentPosition();
      stepper_z.setCurrentPosition(real_pos_z - offset_z_mask);
      offset_x = offset_x_mask;
      offset_y = offset_y_mask;
      offset_z = offset_z_mask;

    }else
    if (a == 221) {
      long real_pos_x = offset_x - stepper_x.currentPosition();
      stepper_x.setCurrentPosition(-real_pos_x + offset_x_drill);

      long real_pos_y = offset_y - stepper_y.currentPosition();
      stepper_y.setCurrentPosition(-real_pos_y + offset_y_drill);

      long real_pos_z = offset_z + stepper_z.currentPosition();
      stepper_z.setCurrentPosition(real_pos_z - offset_z_drill);

      offset_x = offset_x_drill;
      offset_y = offset_y_drill;
      offset_z = offset_z_drill;
    }else
    if (a == 231) {
      long real_pos_x = offset_x - stepper_x.currentPosition();
      stepper_x.setCurrentPosition(-real_pos_x + offset_x_edge);

      long real_pos_y = offset_y - stepper_y.currentPosition();
      stepper_y.setCurrentPosition(-real_pos_y + offset_y_edge);

      long real_pos_z = offset_z + stepper_z.currentPosition();
      stepper_z.setCurrentPosition(real_pos_z - offset_z_edge);

      offset_x = offset_x_edge;
      offset_y = offset_y_edge;
      offset_z = offset_z_edge;
    }else

    if (a == 3) {
      float x = (float(stepper_x.currentPosition())/steps_per_mm_xy);  
      float y = (float(stepper_y.currentPosition())/steps_per_mm_xy);
      float z = (float(stepper_z.currentPosition())/steps_per_mm_z);
      Serial.println(F(""));
      Serial.print(F("X:"));
      Serial.println(-x);
      Serial.print(F("Y:"));
      Serial.println(-y);
      Serial.print(F("Z:"));
      Serial.println(z);
      Serial.print(F("tr_X:"));
      Serial.println(-x + float(float(offset_x)/steps_per_mm_xy));
      Serial.print(F("tr_Y:"));
      Serial.println(-y + float(float(offset_y)/steps_per_mm_xy));
      Serial.print(F("tr_Z:"));
      Serial.println(z + float(float(offset_z)/steps_per_mm_z));
      Serial.print(F("stk:"));
      Serial.println(strikes);
    }else
    if (a == 4) {
      if (!enabled) {
        Serial.print(F("\n mtr dis"));
        return;
      }
      home_z2();
    }else
    if (a ==5) {
      if (!enabled) {
        Serial.print(F("\n mtr dis"));
        return;
      }
      alt = false;
      if (plane_probing) {
      find_boundaries("route.cnc");
      probe_corners();
      find_plane(plane_coefficients1, 0);
      find_plane(plane_coefficients2, 1);
      find_plane(plane_coefficients3, 2);
      find_plane(plane_coefficients4, 3);
      }
      file_read("route.cnc");
    } else
    if (a == 50) {
      if (!enabled) {
        Serial.print(F("\n mtr dis"));
        return;
      }
      String path = Serial.readString(); //I should really just ditch the string but I'm lazy
      path.trim();
      char path_arr[16];
      path.toCharArray(path_arr, 16);
      alt = false;
      if (plane_probing) {
        find_boundaries(path_arr);
        probe_corners();
        find_plane(plane_coefficients1, 0);
        find_plane(plane_coefficients2, 1);
        find_plane(plane_coefficients3, 2);
        find_plane(plane_coefficients4, 3);
      }
      file_read(path_arr);
    }
    if (a == 52) {
      if (!enabled) {
        Serial.print(F("\n mtr dis"));
        return;
      }
      file_read("drill.cnc");
    } else
    if (a == 51) {
      if (!enabled) {
        Serial.print(F("\n mtr dis"));
        return;
      }
      file_read("mask.cnc");
    } else
    if (a == 53) {
      if (!enabled) {
        Serial.print(F("\n mtr dis"));
        return;
      }
      file_read("edge.cnc");
    } else
    if (a == 6) {
      if (!SD.begin(10))
        Serial.println(F("SD f"));
    } else
    if (a == 7) {
      File root = SD.open("/");
      while (File entry = root.openNextFile()) {
        Serial.println(entry.name());
      }
    root.close();
    } else
    if(a == 8) {
      if (!enabled) {
        Serial.print(F("\n mtr dis"));
        return;
      }
      update_limit();
      home_z();
      stepper_z.setCurrentPosition(0);
      offset_z = 0;
    } else
    if(a == 9) {
      if (plane_probing) {
        plane_probing = false;
        Serial.print(F("\nProb:off"));
      }
      else {
        plane_probing = true;
        Serial.print(F("\nProb:on"));
      }
    } else
    if(a == 10) {
      ready = true;
      Serial.print(F("\ndebug"));
    } else
    if (a == 11) {
      if (enabled) {
        stepper_x.disableOutputs();
        stepper_y.disableOutputs();
        stepper_z.disableOutputs();
        enabled = false; 
        Serial.print(F("\n mtr dis"));
      }
      else {
        stepper_x.enableOutputs();
        stepper_y.enableOutputs();
        stepper_z.enableOutputs();
        enabled = true; 
        Serial.print(F("\n mtr en"));
      }
    }
  }
}

void update_limit() {
  int mean = 0;
  limit_x = false;
  limit_y = false;
  limit_z = false;
  for (int i = 0; i<10;i++) {
    mean = mean + analogRead(A6);
  }
  mean = mean / 10;
  if (mean <= 400) { //000
    return;
  } 
  if (401 <= mean && mean < 450) { //100 408
    limit_z = true;
    return;
  }
  if (450 <= mean && mean <= 500) { //001 480
    limit_x = true;
    return;
  }
  if (501 <= mean && mean < 580) { //101 640
    limit_x = true;
    limit_z = true;
    return;
  }
  if (580 <= mean && mean <= 670) { //010
    limit_y = true;
    return;
  } 
  if (670 < mean && mean <= 800) { //110
    limit_y = true;
    limit_z = true;
    return;
  }
  if (801 <= mean && mean < 1015) { //011
    limit_x = true;
    limit_y = true;
    return;
  } 
  if (mean >= 1015) { //111
    limit_x = true;
    limit_y = true;
    limit_z = true;  
    return;
  }
}

void readline(char line[]) {
  if (strlen(line) >= 3) { 
		if ((line[0] != 'G' && line[0] != 'M')) //I have to filter out strings that are not commands
			return;
		if (line[1] < '0' || line[1] > '9' || line[2] < '0' || line[2] > '9') //if it starts with G or M followed by two numbers it's probably an actual command
			return;
	  if (line[0] == 'G' && line[1] == '0' && (line[2] == '1' || line[2] == '0')) {	//G1 and G0 (movement)
      if (enabled == false) {
        Serial.print(F("\n mtr dis"));
        return;
      } 
      if (ready) {
//        bool quick = false; 
//        if (line[2] == '0') {
//          quick = true;
//        }
        float move_x = 0;
        float move_y = 0;
        float move_z = 0; 
        float* plane_coefficients;
        int pos_x,pos_y,pos_z;
        pos_x = find_string('X', line);
        pos_y = find_string('Y', line);
        pos_z = find_string('Z', line);
        if ((pos_x <0) && (pos_y < 0) && (pos_z < 0))
          return;
        int moves = 0;
        long old_z = 0;
        long move_x_y_z[3];
        move_x_y_z[0] = stepper_x.currentPosition();
        move_x_y_z[1] = stepper_y.currentPosition();
        move_x_y_z[2] = stepper_z.currentPosition();
        if (plane_probing) {
          int plane = which_plane(move_x_y_z);
          if (plane == 1) {
            plane_coefficients = plane_coefficients1;
          } else
          if (plane ==2) {
            plane_coefficients = plane_coefficients2;
          } else
          if (plane == 3) {
            plane_coefficients = plane_coefficients3;
          } else
          if (plane == 4) {
            plane_coefficients = plane_coefficients4;
          }
          float x_mm = -((float)move_x_y_z[0]) / steps_per_mm_xy;
          float y_mm = -((float)move_x_y_z[1]) / steps_per_mm_xy;
          float z_comp = x_mm * plane_coefficients[0] + 
               y_mm * plane_coefficients[1] + 
               plane_coefficients[2] + 0.5;
        old_z = z_comp;
        }

        if(pos_x > 0) {
          moves++;
          char* sub_x = &line[pos_x + 1];
          move_x = atof(sub_x);
          if(((offset_x + move_x*steps_per_mm_xy) < max_x*steps_per_mm_xy) && ((offset_x + move_x*steps_per_mm_xy) >= 0)) {
            move_x_y_z[0] = (-move_x)*steps_per_mm_xy;
          } else {
            Serial.println(F("out X"));
            strikes++;
          }
        }

        if(pos_y> 0) {
          moves++;
          char* sub_y = &line[pos_y + 1];
          move_y = atof(sub_y);
          if(((offset_y + move_y*steps_per_mm_xy) < max_y*steps_per_mm_xy) && ((offset_y + move_y*steps_per_mm_xy) >= 0)) {
            move_x_y_z[1] = (-move_y)*steps_per_mm_xy;
          }else {
            strikes++;
            Serial.println(F("out Y"));
          }
        }
        
        if(pos_z> 0) { 
          moves++;
          char* sub_z = &line[pos_z + 1];
          move_z = atof(sub_z);
          if(((offset_z + move_z*steps_per_mm_z) > min_z*steps_per_mm_z) && ((offset_z + move_z*steps_per_mm_z) <= 0)) {
            move_x_y_z[2] = ((move_z)*steps_per_mm_z + float(old_z));
          }else {
            strikes++;
            Serial.println(F("out Z"));
          }
        }
        if((pos_z < 0) && (offset_z != 0) && (is_probed) && (plane_probing)) {
          int plane = which_plane(move_x_y_z);
          if (plane == 1) {
            plane_coefficients = plane_coefficients1;
          } else
          if (plane == 2) {
            plane_coefficients = plane_coefficients2;
          } else
          if (plane == 3) {
            plane_coefficients = plane_coefficients3;
          } else
          if (plane == 4) {
            plane_coefficients = plane_coefficients4;
          }
          moves++;
          long new_z;
          float x_mm = -((float)move_x_y_z[0]) / steps_per_mm_xy;
          float y_mm = -((float)move_x_y_z[1]) / steps_per_mm_xy;
          float z_comp = x_mm * plane_coefficients[0] + 
               y_mm * plane_coefficients[1] + 
               plane_coefficients[2] + 0.5;
        new_z = z_comp;
          move_x_y_z[2] = move_x_y_z[2] - old_z + new_z;  
        }
        int z_s;
        if (line[2] == '0') {
          stepper_x.setSpeed(x_y_speed0);
          stepper_y.setSpeed(x_y_speed0);
          stepper_z.setSpeed(z_speed0);
          stepper_x.setMaxSpeed(x_y_speed0+1);
          stepper_y.setMaxSpeed(x_y_speed0+1);
          stepper_z.setMaxSpeed(z_speed0+1);
          z_s = z_speed0;
        } else {
          stepper_x.setSpeed(x_y_speed1);
          stepper_y.setSpeed(x_y_speed1);
          stepper_z.setSpeed(z_speed1);
          stepper_x.setMaxSpeed(x_y_speed1+1);
          stepper_y.setMaxSpeed(x_y_speed1+1);
          stepper_z.setMaxSpeed(z_speed1+1);
          z_s = z_speed1;
        }
          if(stepper_x.currentPosition() > move_x_y_z[0]) { //if this is true it will be going away from the switch
            if (x_backlash == false) {
              long c_p_x = stepper_x.currentPosition();
              move_now(1, -x_m_backlash);
              stepper_x.setCurrentPosition(c_p_x);
            }
            x_backlash = true;
          }else if (stepper_x.currentPosition() < move_x_y_z[0]){
            if(x_backlash == true) {
              long c_p_x = stepper_x.currentPosition();
              move_now(1, x_m_backlash);
              stepper_x.setCurrentPosition(c_p_x);
            }
            x_backlash = false;
          }

          if(stepper_y.currentPosition() > move_x_y_z[1]) { //if this is true it will be going away from the switch
            if (y_backlash == false) {
              long c_p_y = stepper_y.currentPosition();
              move_now(2, -y_m_backlash);
              stepper_y.setCurrentPosition(c_p_y);
            }
            y_backlash = true;
          }else if (stepper_y.currentPosition() < move_x_y_z[1]){
            if(y_backlash == true) {
              long c_p_y = stepper_y.currentPosition();
              move_now(2, y_m_backlash);
              stepper_y.setCurrentPosition(c_p_y);
            }
            y_backlash = false;
          }
/*
          if(stepper_z.currentPosition() > move_x_y_z[2]) { //if this is true it will be going away from the switch
            if (z_backlash == false) {
              long c_p_z = stepper_z.currentPosition();
              move_now(3, -z_m_backlash);
              stepper_z.setCurrentPosition(c_p_z);
            }
            z_backlash = true;
          }else if (stepper_z.currentPosition() < move_x_y_z[2]){
            if(z_backlash == true) {
              long c_p_z = stepper_z.currentPosition();
              move_now(3, z_m_backlash);
              stepper_z.setCurrentPosition(c_p_z);
            }
            z_backlash = false;
          }
*/
        if (moves > 1) {
          steppers.moveTo(move_x_y_z);
          steppers.runSpeedToPosition();
          stepper_x.setCurrentPosition(move_x_y_z[0]);  
          stepper_y.setCurrentPosition(move_x_y_z[1]);
          stepper_z.setCurrentPosition(move_x_y_z[2]);
        }else {
          if (pos_x > 0)
            stepper_x.moveTo(move_x_y_z[0]);
          if (pos_y > 0)
            stepper_y.moveTo(move_x_y_z[1]);
          if (pos_z > 0)
            stepper_z.moveTo(move_x_y_z[2]);
          stepper_z.setSpeed(z_s);
          while (stepper_x.isRunning() || stepper_y.isRunning() || (stepper_z.distanceToGo() != 0)) {
            stepper_x.run();
            stepper_y.run();
            stepper_z.runSpeedToPosition();
          }
        }
      }else {
      Serial.println(F("Home!"));
      alt = true;
      return;
      }
    } else
    if (line[0] == 'G' && line[1] == '2' && line[2] == '8') {	//G28 (auto-home)
      if (!enabled) {
        Serial.print(F("\n mtr dis"));
        return;
      }
      update_limit(); 
      home_z(); 
      home_x();
      home_y();
      stepper_x.setCurrentPosition(0);
      stepper_y.setCurrentPosition(0);
      stepper_z.setCurrentPosition(0);
      offset_x = 0;
      offset_y = 0;
      offset_z = 0;
      ready = true; 
//      saveData();
    }else
    if (line[0] == 'M' && line[1] == '0' && line[2] == '3') {	//M3 
      digitalWrite(A4, HIGH);
    }else
    if (line[0] == 'M' && line[1] == '0' && line[2] == '5') {	//M5 
      digitalWrite(A4,LOW);
    }else
    if (line[0] == 'M' && line[1] == '2' && line[2] == '2' && line[3] == '0') {
  char* numPtr = strchr(line, ' ');
      if (numPtr != NULL) {
        if (numPtr[1] == 'S' || numPtr[1] == 's') {
          numPtr++;
         }
        int a = atoi(numPtr + 1);  // converte il numero dopo lo spazio
        if (a >= 0 && a <= 100) {
          x_y_speed1 = (long)x_y_speed0 * a / 100;
          Serial.print(F("\n New spd set to "));
          Serial.println(x_y_speed1);
        }
      }
    }
  }
}

int find_string(char car, char line[]) {
	int i; 
	i = 0;
	while(line[i] != '\0') {
		if (line[i] ==  car)
			return i;
		i++;
	}
	return -1;
}

void home_x() {
  stepper_x.setSpeed(700);
  while (!limit_x) {
    stepper_x.runSpeed();
    update_limit();         
  }
  stepper_x.stop();
  stepper_x.setSpeed(x_y_speed0);
  x_backlash = false;
}
void home_y() {
  stepper_y.setSpeed(700);
  while (!limit_y) {
    stepper_y.runSpeed();
    update_limit();         
  }
  stepper_y.stop();
  stepper_y.setSpeed(x_y_speed0);
  y_backlash = false;
}

void home_z() {
  stepper_z.setSpeed(700);
  while (!limit_z) {
    stepper_z.runSpeed();
    update_limit();         
  }
  stepper_z.stop();
  stepper_z.setSpeed(z_speed0);
  z_backlash = false;
}

void home_z2() {
  digitalWrite(A5,HIGH);
  delay(10);
  stepper_z.setSpeed(-z_speed0);
  while((analogRead(A7) >= 700) && ((stepper_z.currentPosition()+offset_z) > min_z*steps_per_mm_z)) {
    stepper_z.runSpeed();
  }
  stepper_z.stop();
  stepper_z.setSpeed(z_speed0);
  if (z_backlash == false) {
  long tmp = stepper_z.currentPosition();
  stepper_z.setCurrentPosition(tmp - z_m_backlash);
  }
  z_backlash = true;
  digitalWrite(A5,LOW);
}
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

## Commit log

2025-09-28 Initial commit
    Update README.md
    Add files via upload
    Update README.md
    Update README.md
    Update README.md
    Update README.md
    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
    [Bed.stl, Preview.blend, Preview_x.blend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]
2026-01-30 Fix speed calculation to handle long values
    [CNC_PCB_release.ino]
